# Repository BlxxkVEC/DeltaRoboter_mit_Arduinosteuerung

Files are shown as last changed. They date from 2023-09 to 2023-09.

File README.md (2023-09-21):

# DeltaRoboter_mit_Arduinosteuerung
 Ein Deltaroboter mit vielen Bauteilen aus dem 3D-Drucker mit einem Arduino zur Steuerung.

## README 

In diesem Repository sind alle Informationen und Dateien zu finden, um einen Deltaroboter (auch Plotbot genannt) zu bauen und mit einer grundlegenden Programmierung auszustatten. Dieses Projekt wurde nicht neu entwickelt, sondern es besteht eine grundlegende Bauanleitung von der Firma "B&R Industrial Automation". Diese beinhaltete jedoch viele preisintensive Bauteile und die Umsetzung war teilweise sehr umständlich. Daher haben wir einige Änderungen vorgenommen und eine neue Schritt-für-Schritt-Bauanleitung verfasst, mithilfe derer jeder das Projekt so durchführen kann, wie wir es getan haben. Die Bauanleitung enthält dafür die Links zu allen Bauteilen und eine detaillierte Beschreibung des Aufbaus. Zusätzlich gibt es eine Projektdokumentation, in welcher auf Schwierigkeiten und vorgenommene Änderungen eingegangen wird. In dem Ordner "3D Modelle" sind alle .stl-Dateien zu finden, die zum fertigen der Bauteile nötig sind. Diese Bauteile sind alle, welche wir in unserem Aufbau verwendet haben.
Bei dem Programm handelt es sich um ein Vorführprogramm. Dabei wird ein metallisches Objekt in Dauerschleife zwischen zwei Punkten umhertransportiert.

Der Ordner "Originaldateien von B&R" enthält alle Informationen und Dateien, welche wir anfangs von B&R erhalten haben, auf Grundlage derer der Roboter und dieses Projekt entstanden ist. Der Ordner enthält die originalen 3D-Modelle (wir haben diese umgearbeitet und Neue hinzugefügt), Zeichnungen von Bauteilen und die Bauanleitung, sowie den Guide für die Software. Der Ordner "Softwarebestandteile" beinhaltet das aktuelle Programm und praktische Bibliotheken für weitere Programme. Im Ordner "Informationsmaterial" sind ergänzende Dokumente zur Arbeitserleichterung enthalten.

Zusätzlich zu den .pdf-Varianten des Belegs und der Projektdokumentation sind hier auch die Links zum Anschauen der Dateien in Overleaf:

Projektdokumentation (Bauanleitung): https://de.overleaf.com/read/rbvrqmyprjpc

Beleg: https://de.overleaf.com/read/dvmrvychqrgd
komplett oben

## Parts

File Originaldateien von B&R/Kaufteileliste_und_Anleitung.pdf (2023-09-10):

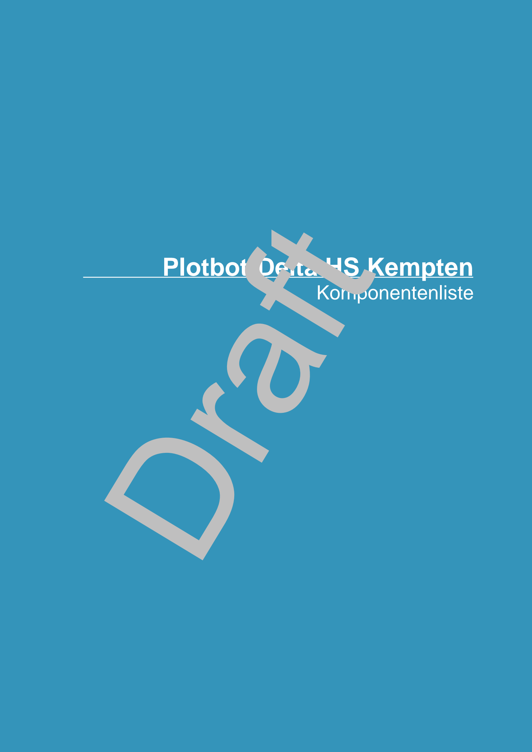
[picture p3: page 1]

# Plotbot-Delta HS Kempten

# Komponentenliste

## Inhaltsverzeichnis

## I Inhaltsverzeichnis

## Einleitung

## 1 Einleitung

Das folgende Dokument enthält Informationen zu den notwendigen Komponenten sowie zum Aufbau des 3 bzw. 4-Achsigen „Plotbot-Delta-Roboters“ der Hochschule Kempten.

Das Dokument wird frei verteilt und dient dem Leser als Anhaltspunkt für die Reproduktion des genannten Delta-Roboters. Das Dokument hat keinen Anspruch auf Vollständigkeit. Für die Richtigkeit der Angaben genauso wie für evtl. Schäden wird keinerlei Haftung übernommen.

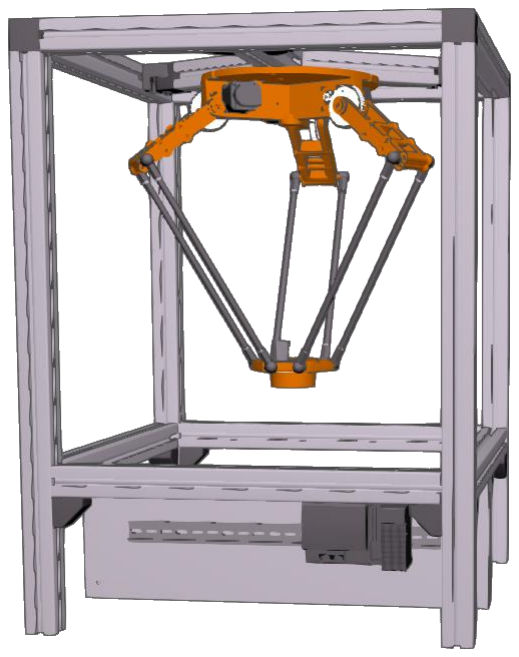
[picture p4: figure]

## 2 Informationen zum Druck der Bauteile

- Der getestete Drucker ist von der Marke Raise3D
- Das verwendete Filament ist PLA. (Alternativ: ABS, PETG, PLA plus)

### - Layerhöhe 0,15-0,2 (filigrane Teile) und 0,25-0,3 für die großen Strukturen - Schalenbreite: 1,2-1,6 mm - Füllgrad: 20-25 % mit kubischem Infill

## 3 Notwendige Komponenten

### 3.1 Liste der Zukaufteile

### 3.1.1 Sensoren

Nr. | Kompo-
nenten

Verwendung

Bezeichnung

Anzahl

Quelle | Preis
Summe
Stand
04.2020

### 1.1 Induktiver

Sensor

Referenzsensor der
Achsen

Autosen
AI811

3 https://autosen.com

58,59€

## Notwendige Komponenten

### 3.1.2 Zahnräder

Nr. | Kompo-
nenten

Verwendung

Bezeichnung

Anzahl

Quelle | Preis
Summe
Stand
04.2020
2.1 Zahnrad | groß | Unterset-zung Motor | Mädler 29405000 | 3 | www.maedler.de | 35,07€
2.2 Zahnrad | klein | Unterset-zung Motor | Zipperle SH12521HF | 3 | www.zipperle.de | 10,16€

### 3.1.3 Gleitlager und Kugelköpfe

Nr. | Komponen-
ten

Verwendung

Bezeichnung

Anzahl

Quelle | Preis
Summe
Stand
04.2020
3.1 Anlaufschei- | ben | Lagerung Gelenk 1 | igus JTM-1420-015 | 6 | www.igus.de | 16,32€
3.2 Kugelge- | lenke | Gelenke CFK Stangen | igus WGRM-08 | 12 | www.igus.de | 23,88€

### 3.1.4 CFK Stangen

Nr. | Komponen-
ten

Verwendung

Bezeichnung

Anzahl

Quelle | Preis
Summe
Stand
04.2020

### 4.1 CFK Stan-

gen

Kohlefaser-Rohr
10x8mm
1000 mm
(z.B.
Graupner
5221.10.8)

Zuschnitt
auf 300mm

2 Diverse Onlinehändler (z.B. http://www.dra- chen- markt.de/epages/DRA- CHEN- MARKT.sf/de_DE/?Ob- jectPath=/Shops/DRA- CHENMARKT/Pro- ducts/200-242)

30,96€

### 3.1.5 Kleber

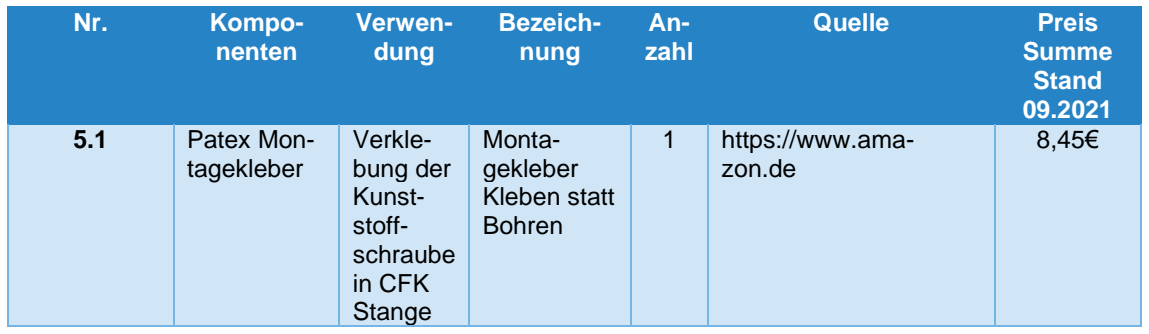
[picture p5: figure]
Kompo-; nenten; Verwen- dung; Bezeich- nung; An- zahl; Quelle; Preis; Summe Stand 09.2021; 5.1 Patex Mon- tagekleber; Verkle- bung der Kunst- stoff- schraube in CFK Stange; Monta- gekleber Kleben statt Bohren; https://www.ama-; zon.de

## Notwendige Komponenten

### 3.1.6 Schrauben

Nr. | Komponen-
ten

Verwendung

Bezeichnung

Anzahl | Quelle | Preis Summe Stand
| | 04.2020
6.1 Senkkopf- | schrauben | | M3X10 | 42
6.2 Senkkopf- | schrauben | | M3X16 | 42
6.3 Zylinder- | schrauben | | M4X45 | 9
6.4 Maden- | schrauben | Rizel -Mo-tor Siche-rung + | M3X4 DIN 916 | 6
6.5 | Zylinderstift | 1014-128 | A 3X16 DIN 7 | 3 - 6 | www.we-gertseder.com/
6.6 Kunststoff- | schrauben | Verbin-dung Ku-gelgelenk-Car-bonstab | DIN 933 M8X35 Kunststoff | 12 | https://www.horn-bach.de/shop/Sec hskantschraube-DIN-933-M8x35-mm-Polyamid-100-Stu-eck/8699894
6.7 Sechskant- | mutter (POM) | Feststel-lung / mi-nimale Einstel-lung der Länge | DIN 934 M8 Kunststoff | 12 | https://www.horn-bach.de/shop/Sec hskantmutter-DIN-934-M8-Poly-amid-50-Stu-eck/8682488

Kommentar – Anlaufscheiben: Die Anlaufscheiben sind dafür gedacht, dass die Kunststoffteile nur an einer kleinen reibungsarmen Fläche beim Betrieb in Kontakt kommen. Ohne würde der Kunststoff zu sehr bremsen.

### 3.1.7 Optionale Teile bei 4-Achs-Version

Nr. | Komponenten | Ver- wen- dung
Bezeichnung | An-
zahl
Quelle | Preis
Summe
Stand
04.2020
7.1 Ritzel | (POM) | Mädler 28202000 | 1 | https://www.ma-edler.de/Ar-ticle/28202000 | 0,63€
7.2 Zahnkranz | (POM) | Mädler 28204000 | 1 | https://www.ma-edler.de/Ar-ticle/28204000 | 1,30€
7.3 | Sicherungsring | Sicherungs-ring DIN 471 20mm | 1 | https://www.ma-edler.de/Ar-ticle/61742000 | 0,31€
7.4 | Motor | Nanotec Schrittmotor Nema 8 mit Stecker SC2018S0604 | 1 | https://de.nano-tec.com/pro-dukte/1839-sca2018-schritt-motor-mit-ste-cker-nema-8/ | 34,20€

## Notwendige Komponenten

### 7.5 Zylinderkopf-

schrauben

Befestigung
Motor

Größe passend zu verwendetem
Motor

### 3.2 B&R Komponenten

### 3.2.1 B&R Hardware Komponenten

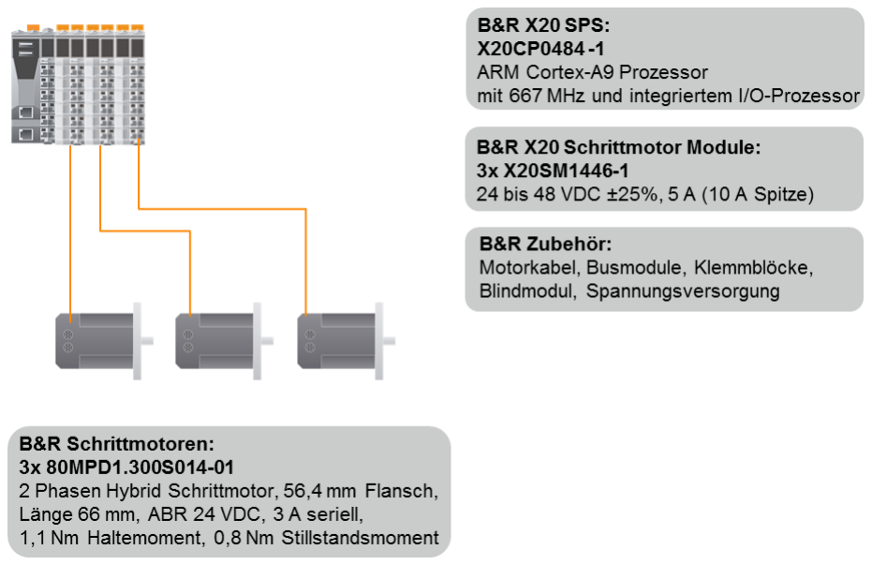
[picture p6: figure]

### 3.2.2 B&R Software Komponenten

- Education Technology Guard Basic Functions GF1460-10
Enthält Lizenzen der Technologiepakete mapp View, mapp Axis und mapp Services
- Education Technology Guard Robotic and CNC Functions MF4610-10
Enthält Lizenzen für eine parallele oder serielle Kinematik mit bis zu 4 bahngesteuerten Achsen
- B&R Automation Studio > 4.7
- mapp Technology > 5.10

### 3.3 Stückliste der 3D-Druck-Bauteile

Nr. | Anzahl | Dateibezeichnung
8.1 | 3 | Arm_Achse_Abstandshalter
8.2 | 3 | Arm_innere_Fuellung
8.3 | 3 | Grundplatte_Teilstück
8.4 | 3 | Steg Grundplatte_links
8.5 | 3 | Steg_Grundplatte_rechts
8.6 | 6 | Arm_Achse_Deckplatte
8.7 | 6 | Arm_seitliche_Platte
8.8 | 1 | Abstützung_Mitte
8.9 | 1 | Parallelplatte_4DOF
8.10 | 1 | Dreheinrichtung
8.11 | 3 | Sicherungsblock

## Notwendige Komponenten

### 3.4 Zu fertigenden Teile

### 3.4.1 Achse aus Aluminium für das erste Gelenk

Anzahl:3

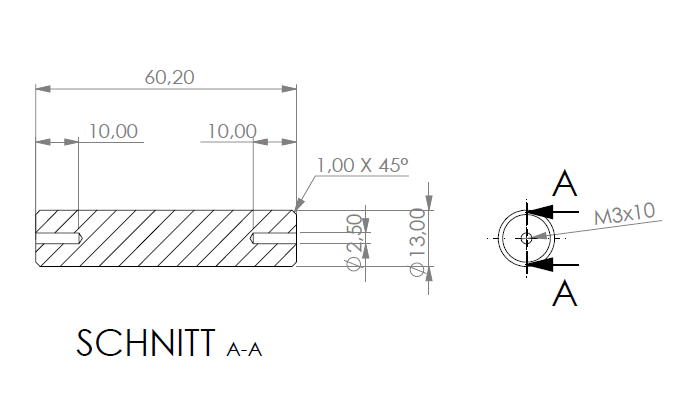
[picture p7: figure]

## Notwendige Komponenten

### 3.5 Zu modifizierende Kaufteile

### 3.5.1 Zahnräder

### 3.5.1.1 Bauteil 2.1 Mädler29405000

Anzahl 3
Die Skizze zeigt den Endzustand des Zahnrads

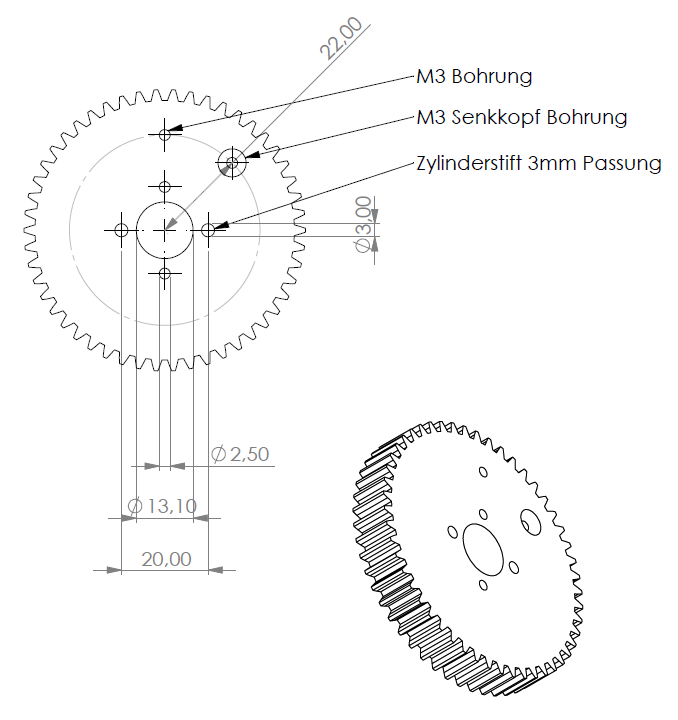
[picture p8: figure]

Kommentar:
Sowohl die „Bohrung M3“ wie auch die „M3 Senkkopf Bohrung“ dienen dem induktiven Sensor als Auslöser. Es ist nur eine der beiden Bohrungen notwendig.
Verwendet man die „M3 Bohrung“ steht der Roboter nach der Referenzfahrt in einer Position mit waagrechten Armen.
Bei Verwendung der anderen Position steht er etwas tiefer. Welche Position verwendet wird ist Geschmackssache.
Gleiches gilt für die Wahl der Schraube. Verwendet man eine Madenschraube, lässt sich diese in montiertem Zustand verstellen, sofern der Schraubenkopf in die dem Motor gegenüberliegende Richtung zeigt. Nachteil: Der Sensor muss auf einen kleineren Gegenstand reagieren. Verwendet man die Senkkopfschraube mit Kopf Richtung Motor. Ist das Schaltobjekt größer allerdings lässt sich die Schraube in montiertem Zustand nicht verstellen.

## Notwendige Komponenten

### 3.5.1.2 Zahnrad Mädler28204000 (Nur bei Verwendung der 4. Achse Notwendig)

Anzahl 1
Die Skizze zeigt den Endzustand des Zahnrads

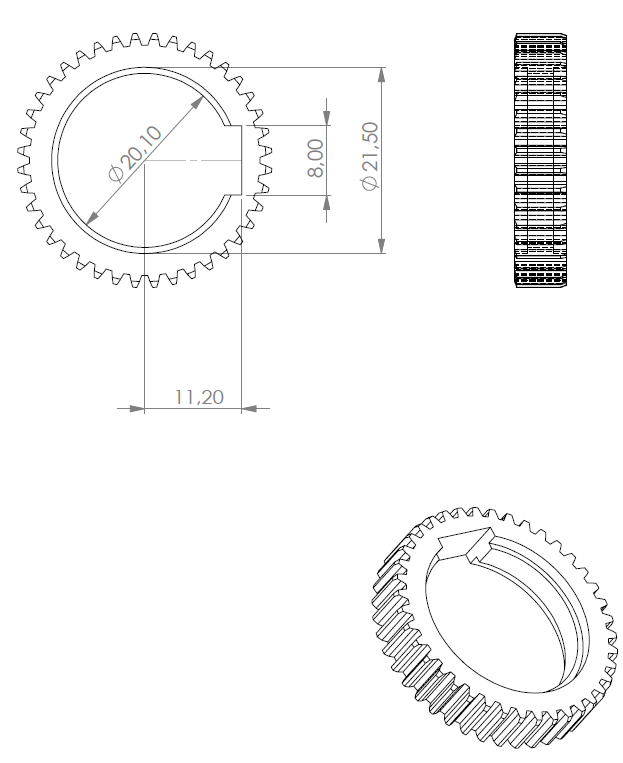
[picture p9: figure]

## Montage des Roboters

### 3.5.2 Sonstige Bauteile

- Evtl. Aufbohren der Zahnräder 2.2 auf das Maß der Motorwellen
- Bohrungen und Gewinde für die Madenschrauben setzen, die die Zahnräder 2.2 auf den Motorwellen arretieren.

## 4 Montage des Roboters

Schritt 1: M3 Gewinde in Steg_Grundplatte_links 8.4 und Steg_Grundplatte_rechts 8.5 schneiden

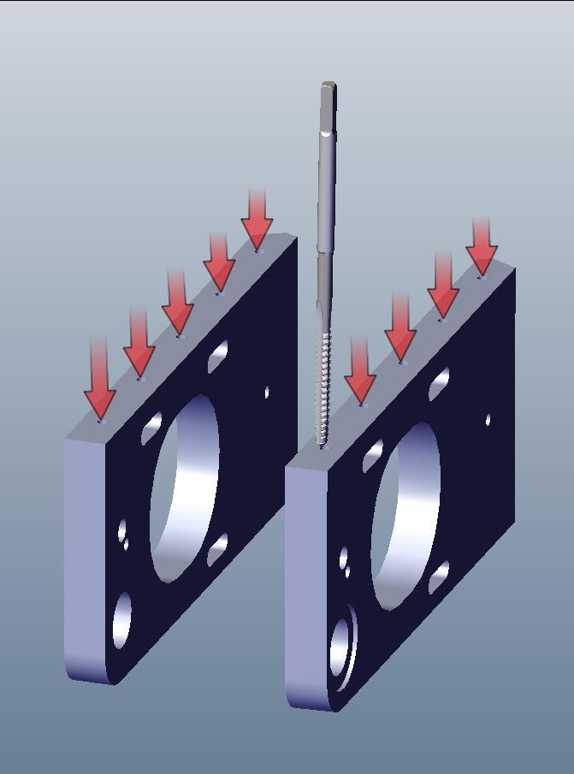
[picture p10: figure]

Schritt 2: Bauteile 8.4 und 8.5 mit Stiften 6.5 miteinander verbinden

Schritt 3 Zusammengefügte Bauteile 8.4 und 8.5 mit der Grundplatte verschrauben


Schritt 4: Abstützung_Mitte 8.8 montieren


Schritt 5: Induktiven Sensor 1.1 und Anlaufscheiben 3.1 montieren

Schritt 6: M3 Gewinde in Bauteil Arm_innere_Füllung 8.2 schneiden


Schritt 7: Bauteil 8.2 mit Arm_seitliche_Platte 8.7 (M3X10) und bearbeitetem Zahnrad 2.1 (M3X16 und Zylinderstift 6.5) verschrauben

Schritt 8: Gewinde M8 in Bohrung für Kugelkopf schneiden


Schritt 9: Bauteil Arm_innere_Fuellung 8.2 mit zweitem Bauteil Arm_seitliche_Platte 8.7 (M3X10) und bearbeitetem Zahnrad 2.1 (M3X16 und Zylinderstift 6.5) verschrauben. Dabei Distanzscheibe Arm_Achse_Abstandshalter 8.1 mit einsetzen. Im Anschluss auch auf dieser Seite ein Gewinde M8 vgl. Schritt 8 schneiden.

Schritt 10: Einschrauben der Kugelköpfe.


Schritt 11: Vormontierter Arm mit der Aluminiumachse an der Grundplatte befestigen und die „Arm_Achse_Deckplatte“ 8.6 mit M3X16 Schrauben auf beiden Seiten verschrauben.

Schritt 12: M8 Gewinde in Parallelplatte 8.9 schneiden und Kugelköpfe montieren.


Optional Schritt 13: Nema 8 Motor auf Parallelplatte 8.9 montieren und Zahnrad 7.1 am Motor befestigen. Überarbeitetes Zahnrad 7.2 in Dreheinrichtung 8.10 einpressen. Parallelplatte 8.9 und Dreheinrichtung 8.10 verbinden und mit Sicherungsring 7.3 verbinden.

Schritt 14: Verbinden der CFK Stäbe 4.1 mit den Kugelgelenken 3.2. Dazu werden die Köpfe der Kunststoffschrauben 6.6 abgesägt. Anschließend werden die Kugelgelenke 3.2 komplett auf die Kunststoffschrauben 6.6 geschraubt und von unten mit den Muttern 6.7 gekontert.


Die CFK Stäbe 4.1 werden auf die Länge von 300 mm zugeschnitten und die zuvor vorbereiteten Winkelgelenke 3.2 mit dem Gewinde in die Enden der CFK Stäbe 4.1 verklebt. Beim Verkleben ist auf die Ausrichtung der Winkelgelenke 3.2 zu achten. Diese müssen wie im untenstehenden Bild dargestellt in dieselbe Richtung orientiert sein. Als Kleber kann beispielsweise der Montagekleber von Patex 5.1 verwendet werden. Die verklebten CFK Stäbe 4.1 einen ganzen Tag aushärten lassen.

WICHTIG: Nicht zu viel Kleber auf das Gewinde auftragen, damit die Mutter nicht mit verklebt wird.


Schritt 15: Dreheinheit und Arme des Delta mit den vorbereiteten CFK Stäben inkl. Kugelschalen verbinden.

Schritt 16: Motoren mit aufgesetzten Zahnräder 2.2 in Motorhalterung einsetzen und mit Sicherungsblock 8.11 verschrauben. Dabei den Motor so einstellen, dass die Zahnräder im Eingriff sind.

Montage vollständig


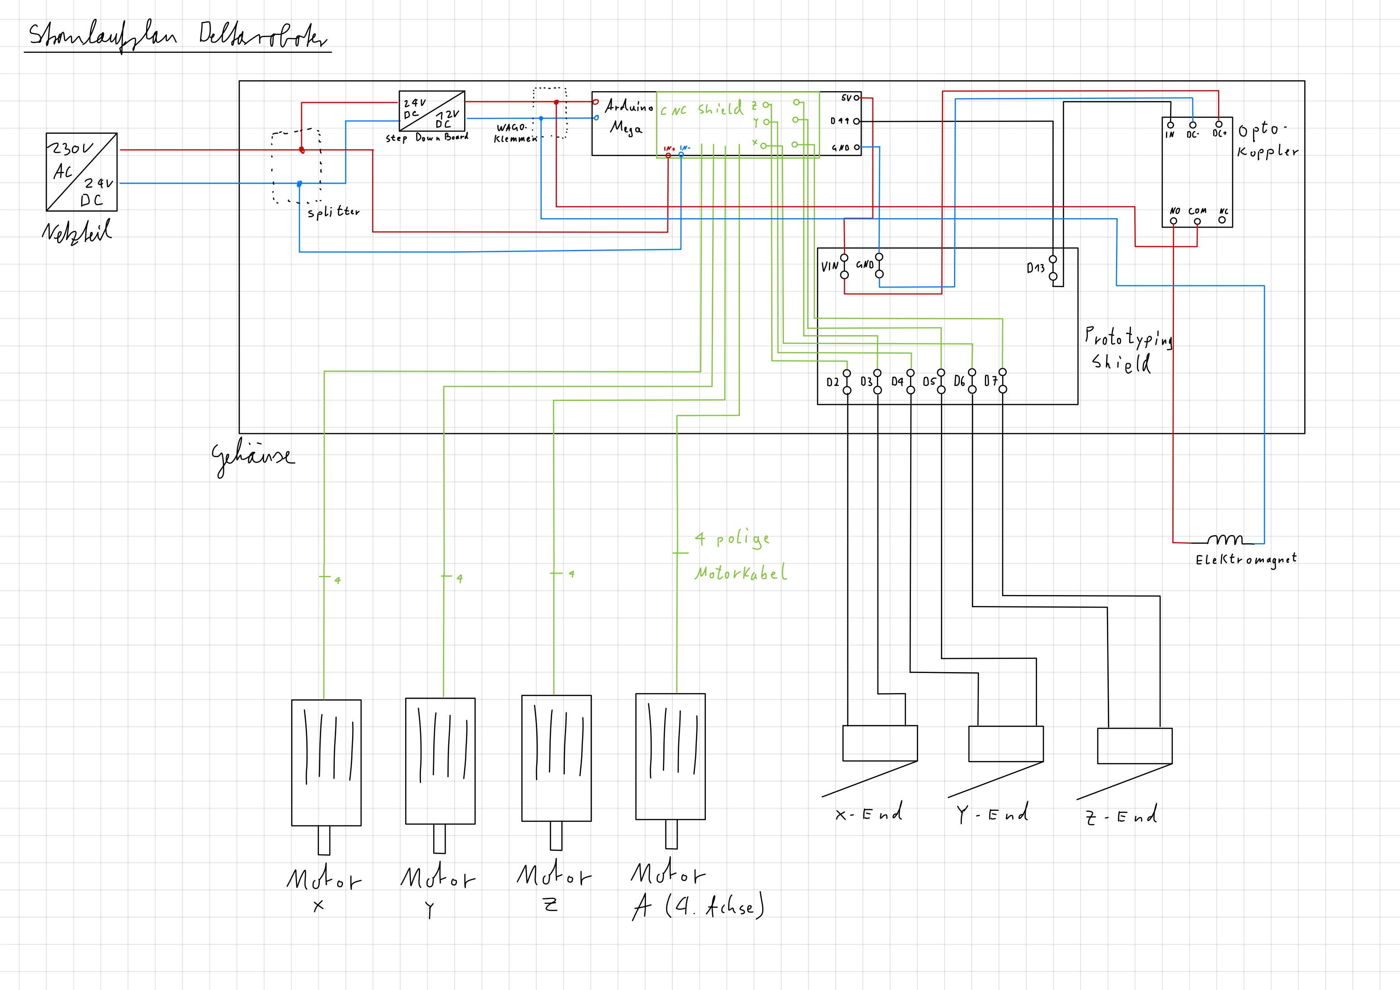
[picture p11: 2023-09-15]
Informationsmaterial/Stromlaufplan Delta-Roboter.jpg

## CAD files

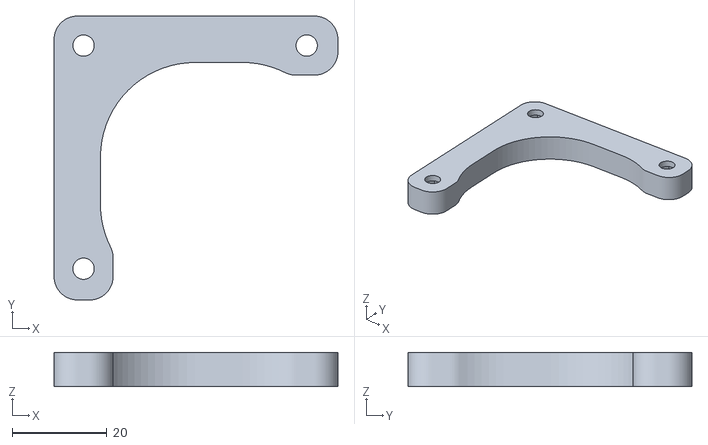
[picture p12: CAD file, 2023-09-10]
Originaldateien von B&R/B&R 3D-Modelle/3xSicherungsblock.STL
60.0 x 60.0 x 7.25

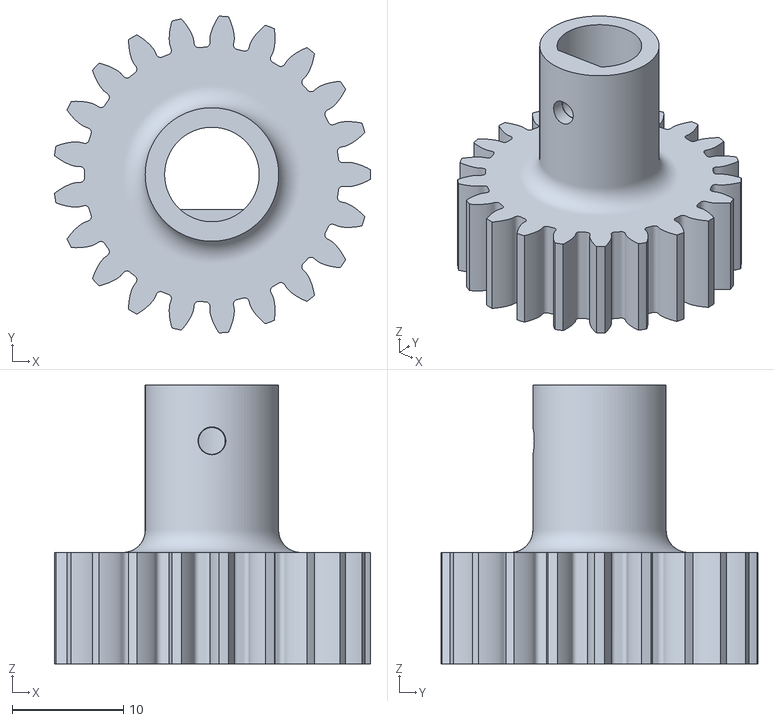
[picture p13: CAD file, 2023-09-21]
verwendete 3D Modelle/3xMotorzahnrad klein 8mm.stl
28.4 x 28.5 x 25.1

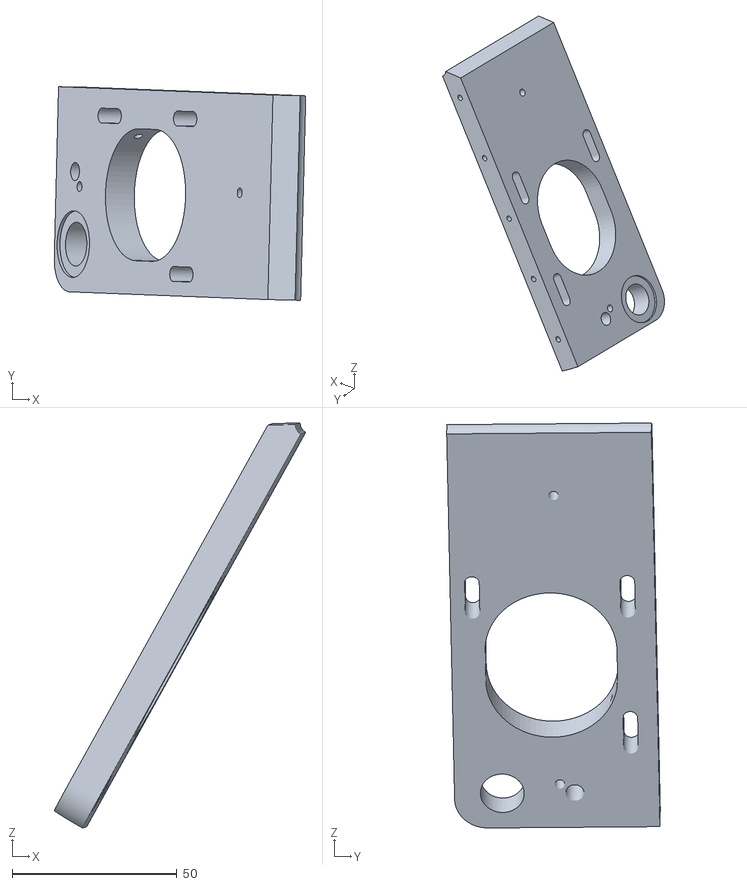
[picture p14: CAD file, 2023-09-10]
Originaldateien von B&R/B&R 3D-Modelle/3xSteg_Grundplatte_rechts.STL
76.2 x 64.7 x 122.7

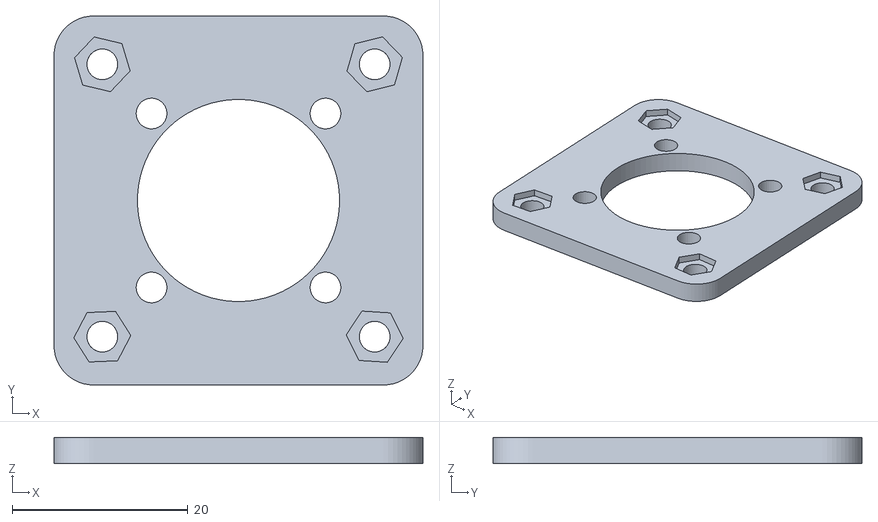
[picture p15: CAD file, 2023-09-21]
verwendete 3D Modelle/3xAdapterplatte Motor Planetengetriebe.stl
42.0 x 42.0 x 3.00

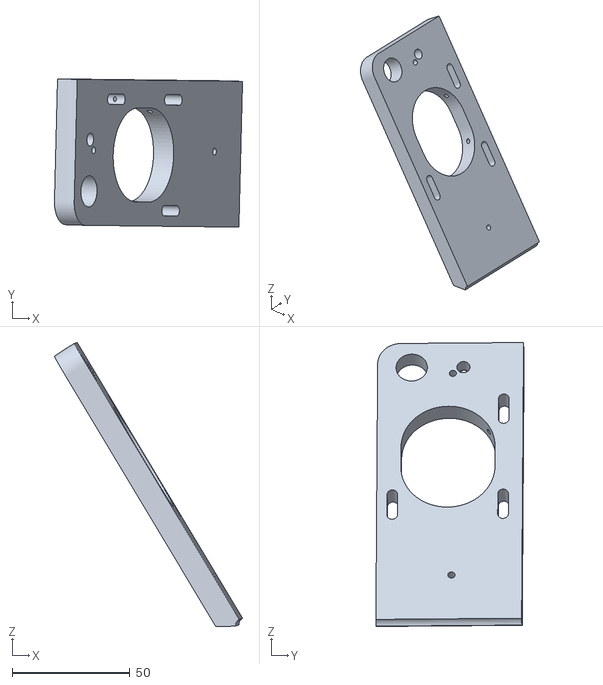
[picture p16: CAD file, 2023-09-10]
Originaldateien von B&R/B&R 3D-Modelle/3xSteg_Grundplatte_links.STL
80.0 x 63.1 x 120.8

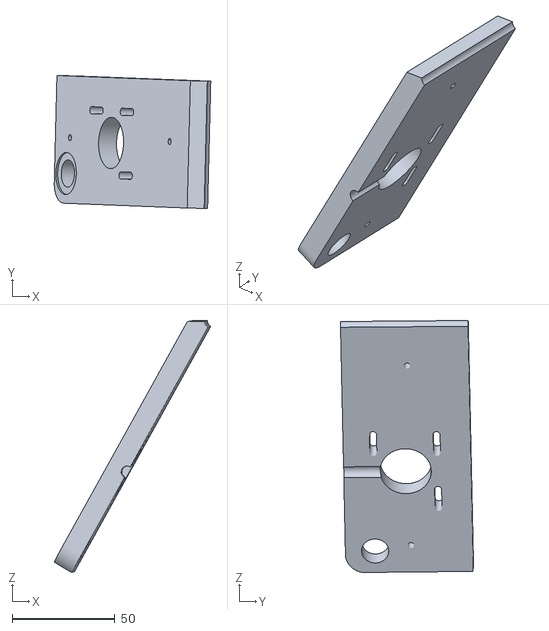
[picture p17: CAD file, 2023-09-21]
verwendete 3D Modelle/3x Motorplatte rechts überarbeitet (M3 zur Motormontage).stl
76.2 x 64.7 x 122.7

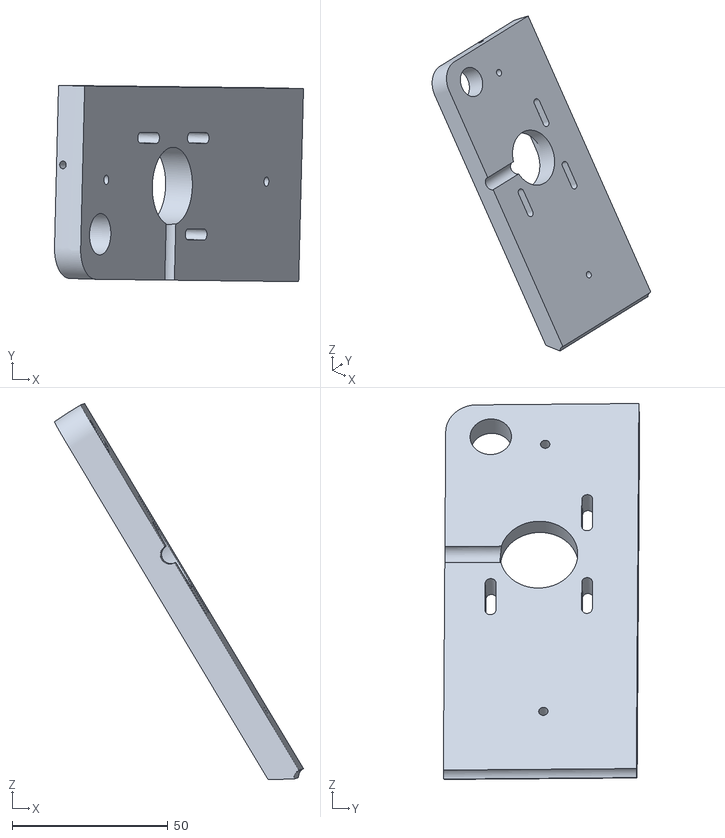
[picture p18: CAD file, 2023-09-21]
verwendete 3D Modelle/3x Motorplatte_links_überarbeitet (M3 zur Motormontage).stl
80.0 x 63.1 x 120.8

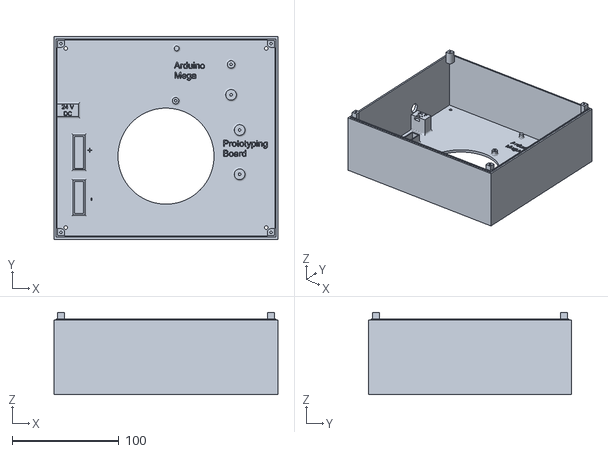
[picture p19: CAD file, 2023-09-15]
verwendete 3D Modelle/Gehäuse Elektronik _Träger.stl
210.0 x 190.0 x 77.0

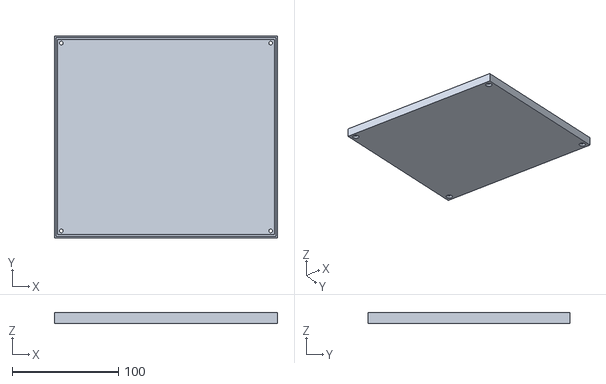
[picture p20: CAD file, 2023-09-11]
verwendete 3D Modelle/Gehäuse Elektronik_Deckel.stl
210.0 x 190.0 x 10.0

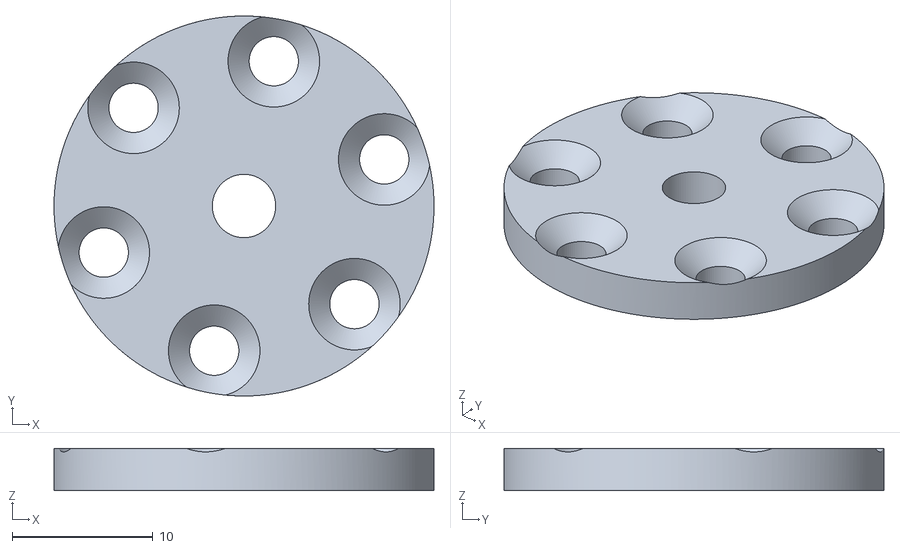
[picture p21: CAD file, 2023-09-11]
verwendete 3D Modelle/Magnethalterung .stl
27.0 x 27.0 x 3.00

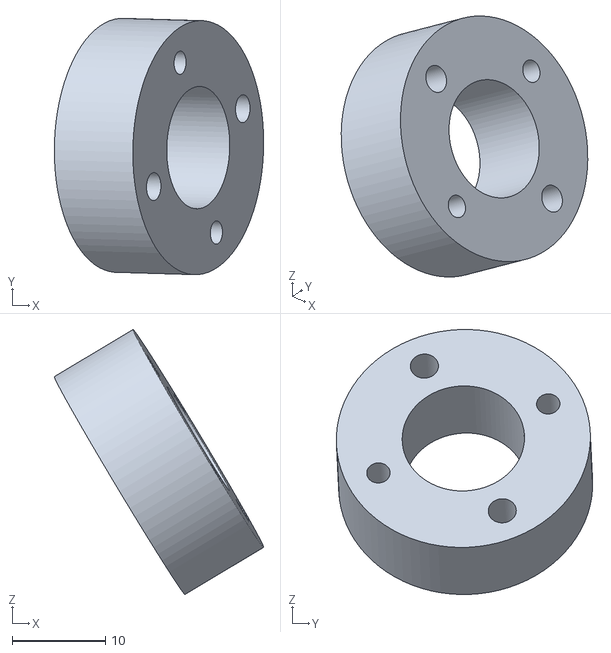
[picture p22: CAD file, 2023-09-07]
verwendete 3D Modelle/3xArm_Achse_Abstandshalter.STL
22.4 x 27.4 x 28.4

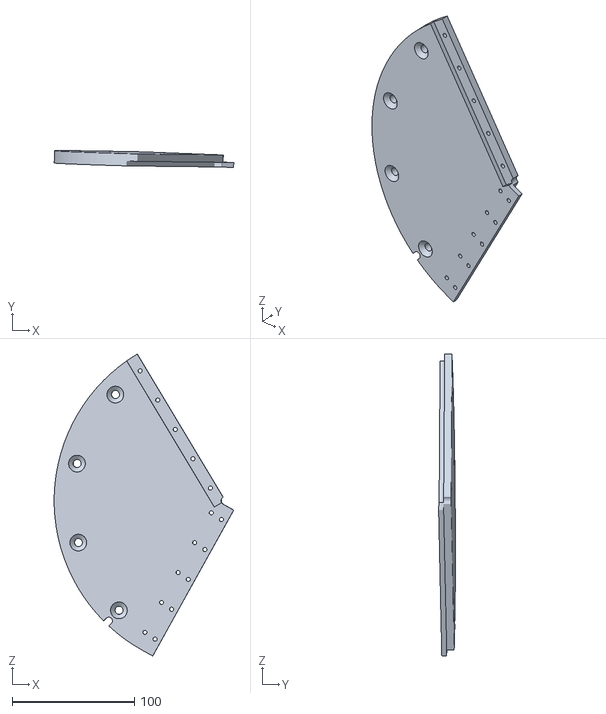
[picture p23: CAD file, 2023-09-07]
verwendete 3D Modelle/3x Trägerplatte_Teilstück.STL
147.1 x 13.8 x 247.4

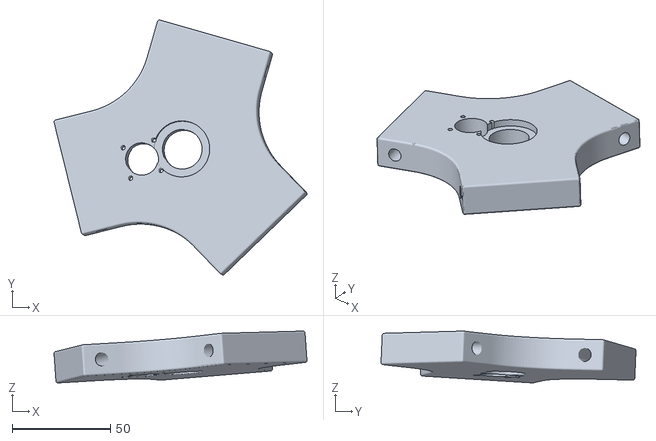
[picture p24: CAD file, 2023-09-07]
verwendete 3D Modelle/Parallelplatte.stl
128.7 x 129.7 x 26.4

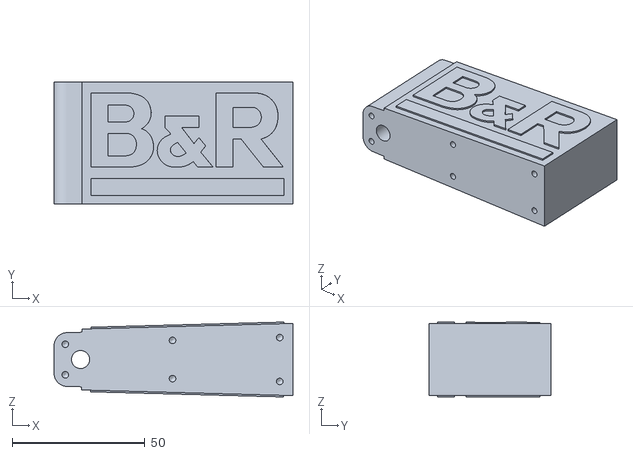
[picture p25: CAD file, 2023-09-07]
verwendete 3D Modelle/3xArm_innere_Fuellung.STL
90.0 x 46.0 x 28.2

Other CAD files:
verwendete 3D Modelle/6xArm_seitliche_Platte.STL
verwendete 3D Modelle/Achse.stl
verwendete 3D Modelle/Armzahnrad 29405000.stl
verwendete 3D Modelle/Zahnkranz (4. Achse).stl
verwendete 3D Modelle/6xArm_Achse_Deckplatte.STL
verwendete 3D Modelle/Abstützung_Mitte.STL
verwendete 3D Modelle/Dreheinrichtung.STL
verwendete 3D Modelle/Motorzahnrad 4. Achse 28202000.stl

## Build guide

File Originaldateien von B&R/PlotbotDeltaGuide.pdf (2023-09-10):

# PlotbotDelta@B&R

# Quick Start Guide

DeltaPlotbot@B&R
Quick Start Guide

Copyright © B&R - Änderungen vorbehalten PlotbotDeltaGuide.docx

14.11.22

B&R behält sich inhaltliche Änderungen ohne Ankündigung vor. Die Haftung durch B&R für drucktechnische Fehler sowie für sämtliche Angaben in diesem Dokument ist - soweit gesetzlich möglich – ausgeschlossen. Der Anwender ist für die Einhaltung aller relevanten und facheinschlägigen Sicherheitsmaßnahmen selbst verantwortlich. B&R weist darauf hin, dass die verwendeten Soft- und Hardwarebezeichnungen sowie Markennamen der jeweiligen Unternehmen den gesetzlichen Schutzvorschriften des Immaterialgüterrechts unterliegen.

Quick Start Guide

## Versionsstände

Version | Datum | Kommentar | Bearbeiter
1.00.0 | 13.11.2020 | Erste Ausgabe | Markus Straßer
2.00.0 | 24.11.2021 | Teach-Funktion, Datei Editor, Teach-Liste in Robotik Programm Konvertierung und laufende Verbesserungen | Markus Straßer

Tabelle 1: Versionsstände

## I Sicherheitshinweise und Symbole

Die Sicherheitshinweise werden im vorliegenden Dokument wie folgt gestaltet:

Warnung: Bei Missachtung der Sicherheitsvorschriften und -hinweise besteht die Gefahr schwerer Verletzungen oder großer Sachschäden.

Vorsicht: Bei Missachtung der Sicherheitsvorschriften und -hinweise besteht die Gefahr von Verletzungen oder von Sachschäden. Wichtige Angaben zur Vermeidung von Fehlfunktionen.

Information: Wichtige Angaben zur Vermeidung von Fehlfunktionen.

Quick Start Guide

## II Allgemeine Warnhinweise

Der Roboter darf nur unter der Berücksichtigung der DIN-EN-ISO 10218 Teil 1 und Teil 2 betrieben werden. Die Normen definieren Sicherheitsmaßnahmen für Industrieroboter wie notwendige Schutzzäune, Notfalleinrichtungen, Zugriffsschutz oder ähnliches.

Alle elektrischen Arbeiten müssen von einer berechtigten Person (Elektrofachkraft) durchgeführt wurden. Die Installation hat grundsätzlich in einem spannungsfreien Zustand zu erfolgen. Bei Missachtung kann es zu Kurzschlüssen oder elektrischen Schlägen kommen.

Sobald das Programm auf die Steuerung übertragen wurde, ist der Roboter in der Lage sich zu bewegen. Sorgen Sie dafür, dass der Roboter befestigt wurde und das keine Personen im Arbeitsbereich des Roboters sind. Ansonsten kann es zu Verletzungen und oder Beschädigungen des Roboters kommen!

Quick Start Guide | Einleitung

## Inhaltsverzeichnis

Quick Start Guide | Einleitung

## 1 Einleitung

In diesem Dokument wird gezeigt, wie man einen parallelen 3-Achs-Delta Roboter mit der B&R Steuerungsplattform und dem Automation Studio Projekt „PlotbotDelta“ in Betrieb nimmt.

## 2 Notwendige Softwareversionen

Software | Version
Automation Studio | V4.10.3.60
Automation Runtime | B4.91
mappMotion | 5.14
mappServices | 5.14
mappCockpit | 5.14
mappView | 5.14
SceneViewer | 4.1.0

Tabelle 2 Notwendige Versionen

## 3 Unterstütze Varianten des Roboters

3-Achs Delta Roboter

Schrittmotoren

Induktionssensoren für Referenzfahrt

Reichweite: 400 mm

Traglast: ca. 1000 g

Variante | Unterstütz

3-Achs Delta Plotbot – Ohne Geber 3-Achs Delta Plotbot – Mit Geber

Tabelle 3 Projekt Varianten

Abbildung 1 PlotbotDelta

Quick Start Guide | Notwendige B&R Komponenten

## 4 Notwendige B&R Komponenten

### 4.1 Hardware Komponenten

Anzahl | Artikelnummer | Optional | Beschreibung | Beschaffung
1 | X20CP0484-1 | | Steuerung | education.de@br-automation.com
1 | X20BB52 | | Busbasismodul
1 | X20PS9600 | | Spannungsversorgung
1 | X20TB12 | | Feldklemme
3 | X20SM1446-1 | | Schrittmotormodul
3 | X20BM31 | | Busmodul
3 | X20TB12 | | Feldklemme
1 | X20DI4371 | | Digitales Eingangsmodul
1 | X20DO6322 | | Digitales Ausgangsmodul
2 | X20BM11 | | Busmodul
2 | X20TB12 | | Feldklemme

Tabelle 4 B&R Komponenten

Die Hardwarekomponenten müssen in der gleichen Reihenfolge wie im Automation Studio Projekt gesteckt werden (siehe Abbildung 2).

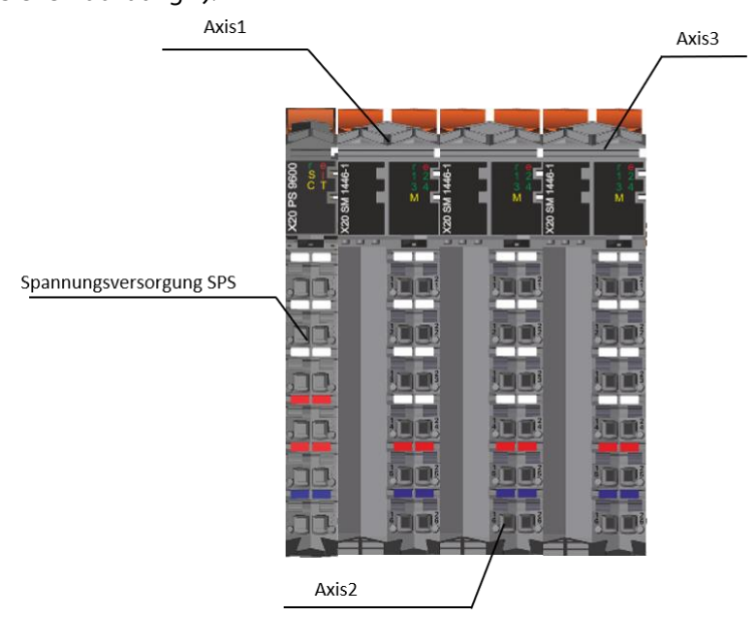
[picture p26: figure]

Abbildung 2: Reihenfolge der Hardwaremodule

### 4.2 B&R Lizenzen

Für den Betrieb des Roboters für Lehr- und Forschungszwecke werden keine Lizenzen verlangt.

Quick Start Guide

Optionale Komponenten für die Spannungsversorgung

## 5 Optionale Komponenten für die Spannungsversorgung

Für einen laborgerechten Einsatz wird empfohlen Niedervoltsteckverbindungen und Tischnetzteile zu verwenden, damit die Komponenten Berührungssicher sind. Sollte der Roboter einen Schaltschrank bekommen, kann auch ein herkömmliches 24V Hutschienen Netzteil und Klemmblöcke zur Spannungsverteilung verwendet werden.

Anzahl | Artikelnummer | Beschreibung | Beschaffung | Link
2 | DC-2G21-XL | Niedervolt Buchse

Conrad Electronic

Elhttps://www.conrad.de/de/p/bkl-electronic-niedervolt-anschlusskabel-niedervolt-buchse-offenes-ende-5-5-mm-2-5-mm-2-00-m-1-st-1082739.html (https://www.conrad.de/de/p/bkl-electronic-niedervolt-anschlusskabel-niedervolt-buchse-offenes-ende-5-5-mm-2-5-mm-2-00-m-1-st-1082739.html)

1 | 1371050 | Niedervolt Y-Verteiler

https://www.conrad.de/de/p/voltcraft-niedervolt-anschlusskabel-niedervoltbuchse-niedervolt-stecker-5-5-mm-2-1-mm-5-5-mm-2-1-mm-1-10-m-1-st-1371050.html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 (https://www.conrad.de/de/p/voltcraft-niedervolt-anschlusskabel-niedervolt-buchse-niedervolt-stecker-5-5-mm-2-1-mm-5-5-mm-2-1-mm-1-10-m-1-st-1371050.html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)

2 | DC14-M | Niedervolt Stecker

https://www.conrad.de/de/p/tru-componentsdc14-m-niedervolt-steckverbinder-stecker-gerade-5-5-mm-2-1-mm-1-st-1570700.html (https://www.conrad.de/de/p/tru-components-dc14-m-niedervolt-steckverbinder-stecker-gerade-5-5-mm-2-1-mm-1-st-1570700.html)

1 | GST280A24-C6P | Tischnetzteil 11,67 A

https://www.conrad.de/de/p/mean-wellgst280a24-c6p-tischnetzteilfestspannung-24-v-dc-11-67-a-280-08-w-1439261.html (https://www.conrad.de/de/p/mean-well-gst280a24-c6p-tischnetzteil-festspannung-24-v-dc-11-67-a-280-08-w-1439261.html)

1 | 1008230 | Kaltgeräte Kabel

https://www.conrad.de/de/p/hawa-1008230-
kaltgeraete-anschlusskabelschwarz-2-00-m-621535.html (https://www.conrad.de/de/p/hawa-1008230-kaltgeraete-anschlusskabel-schwarz-2-00-m-621535.html)
Tabelle 5 Sonstige Komponenten

## 6 Verdrahtung

Alle elektrischen Arbeiten müssen von einer berechtigten Person (Elektrofachkraft) durchgeführt wurden. Die Installation hat grundsätzlich in einem spannungsfreien Zustand zu erfolgen. Bei Missachtung kann es zu Kurzschlüssen oder elektrischen Schlägen kommen.

### 6.1 Spannungsversorgung

Im Folgenden werden die Arbeitsschritte für die Verdrahtung unter Verwendung der optionalen Komponenten aus Kapitel 5 beschrieben:

1. Stecker am Netzteil mit einem Seitenschneider abschneiden. 2,5 – 3,0 cm entmanteln. Die vier Adern des Kabels abisolieren und mit Aderendhülsen versehen.
2. Die Adern in die Niedervolt-Stecker einführen und festschrauben
Pol | Aderfarbe
+ | Rot, Blau
- Weiß, Schwarz

Tabelle 6 Netzteil Adernbelegung

Quick Start Guide | Verdrahtung
3. Um die Niedervolt-Buchsen auf die X20 Module anzubringen, das Kabel auf die gewünschte Länge zuschneiden und das rote Kabel auf Pin 15, sowie das rot-schwarze Kabel auf Pin 16 verbinden.
4. Da das Hardwaresetup aus insgesamt 4 X20 Scheiben besteht, die eine direkte Spannungsversorgung benötigen, aber nur 2 Niedervolt-Buchsen zur Verfügung stehen, müssen zwei der Module per Drahtbrücke versorgt werden. Somit hängt die Spannungsversorgung der SPS und der Achse 1 an einer Zuleitung, sowie die der Achsen 2 und 3.

Die Drahtbrücke wird mittels einer Zwillings-Aderendhülse realisiert. Außerdem ist es notwendig noch eine zusätzliche Drahtbrücke am PS9600 anzubringen (siehe Abbildung 3).

Die rechte Seite der Klemmen wird für die Spannungsversorgung der Induktionssensoren am Roboter genutzt.

Kanal | Aderfarbe | Pin
+24VDC | Rot | 15
GND | Rot-Schwarz | 16

Tabelle 7 Spannungsversorgung X20 Module

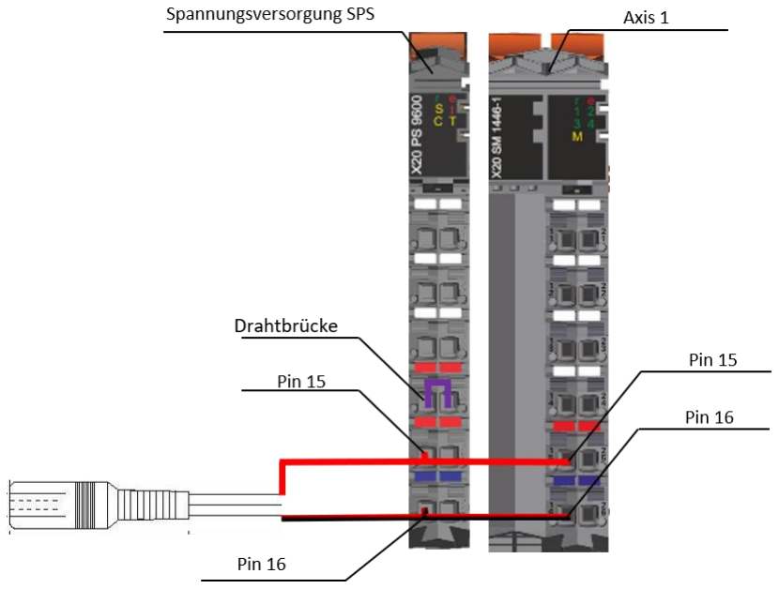
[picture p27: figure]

Abbildung 3: Versorgung SPS und Achse 1

Quick Start Guide | Verdrahtung

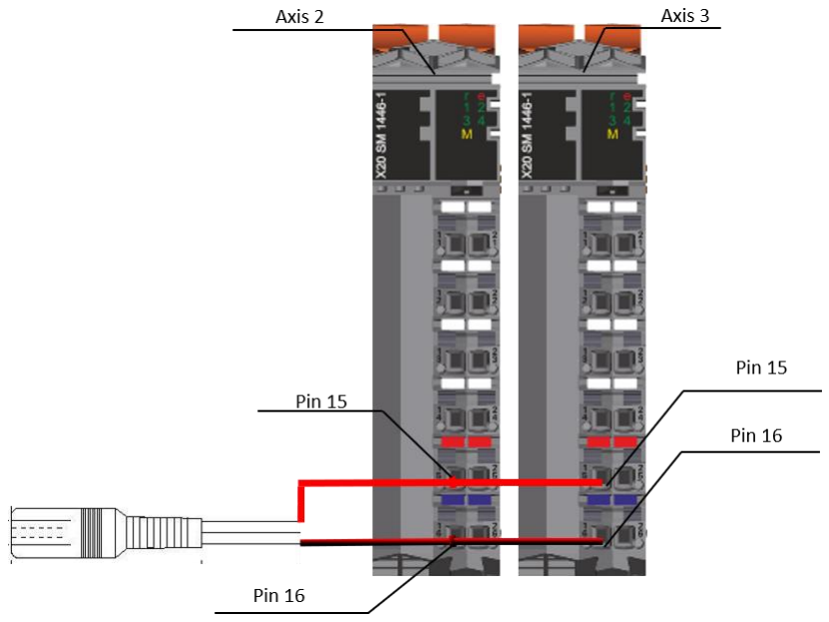
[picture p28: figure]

Abbildung 4: Versorgung Achse 2 und 3

5. Sind alle Arbeitsschritte erledigt kann das Netzteil über den Y-Verteiler mit allen Steckern verbunden werden. Fangen alle Module an grün zu blinken, wurde die Verdrahtung der Spannungsversorgung fehlerfrei durchgeführt.

Alle weiteren elektrischen Arbeiten müssen wieder im spannungsfreien Zustand durchgeführt werden!

### 6.2 Motor

Bei der Verbindung der Motorkabel zu den X20 Schrittmotor Modulen ist darauf zu achten, dass die Achsen in der richtigen Reihenfolge verbunden werden. Je nach Reihenfolge ändert sich die Ausrichtung des Koordinatensystems.
In diesem Dokument werden die Motoren auch als Achsen bzw. als Axis bezeichnet. Als Achse wird dabei nicht nur der Motor selbst, sondern das eigentliche Drehgelenk am Roboter verstanden.

Quick Start Guide | Verdrahtung

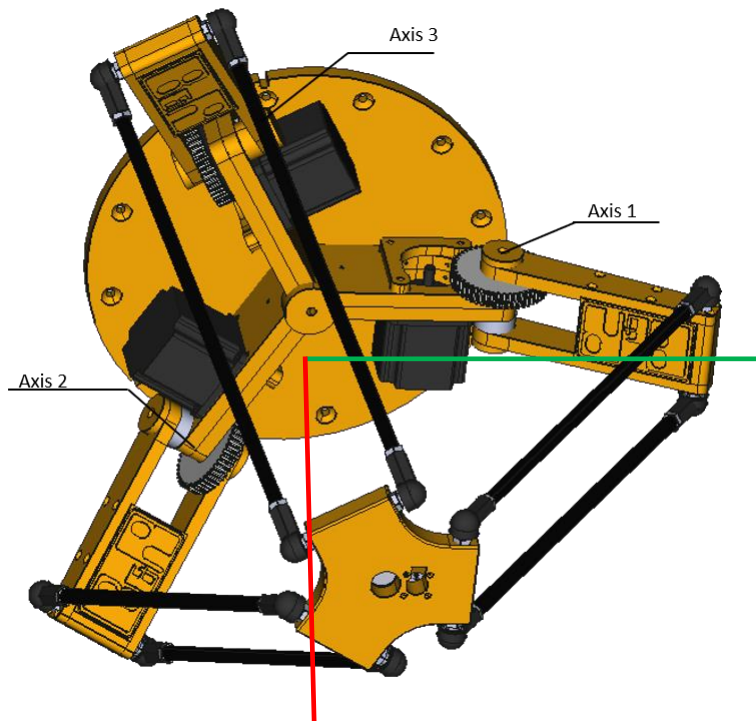
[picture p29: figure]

Abbildung 5 Achsenbezeichnung

Die vier verschiedenen Adern des Konfektionierten B&R Motorkabels müssen wie folgt mit den X20SM1446-1 Modulen verbunden werden.

Kanal | Adernfarbe | Pin
A | Schwarz | 13
A\ | Grau | 23
B | Braun | 14
B\ | Blau | 24

Tabelle 8 Aderbelegung Motoren

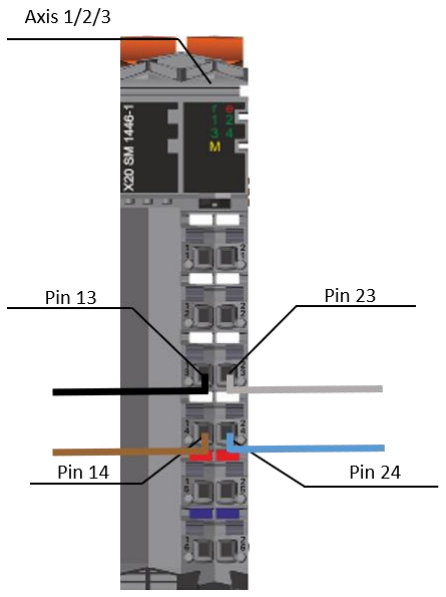
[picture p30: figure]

Abbildung 6 Motoranschluss

Y

X

Quick Start Guide | Verdrahtung

### 6.3 Referenzschalter

Die Kabel der Referenzschalter müssen in die davor vorgesehen Verschraubung am Roboter befestigt werden. Achten Sie darauf, dass die Sensoren der jeweiligen Achsen auf die korrekte X20 Schrittmotorkarte gelegt wird.
Nachdem die Kabel entmantelt und abisoliert wurden müssen diese wie folgt mit der X20SM1446-1 verbunden werden.
Kanal | Adernfarbe | Pin
Signal | Schwarz | 22
+24 VDC | Braun | 25
GND | Blau | 26

Tabelle 9 Belegung Referenzsensoren

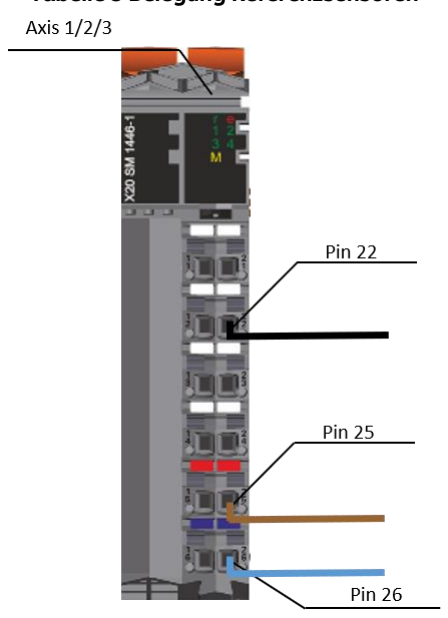
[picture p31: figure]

Abbildung 7 Anschluss Referenzschalter

Quick Start Guide | Mechanische Anpassungen

## 7 Mechanische Anpassungen

In den Standard Einstellungen befindet sich der Ursprung des Koordinaten Systems auf der Höhe der Gelenke des Robotersockels. Sollte sich durch das Anschrauben eines Rahmens die Basishöhe verändern. Kann dies im Automation Studio Projekt angepasst werden.

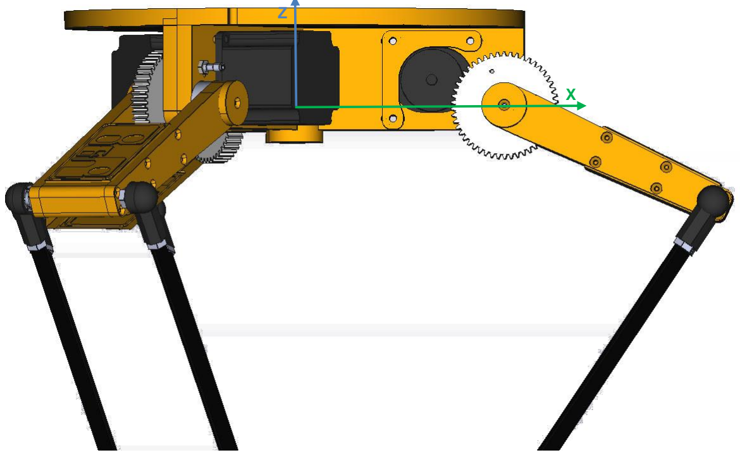
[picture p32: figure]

Abbildung 8 Koordinaten Ursprung

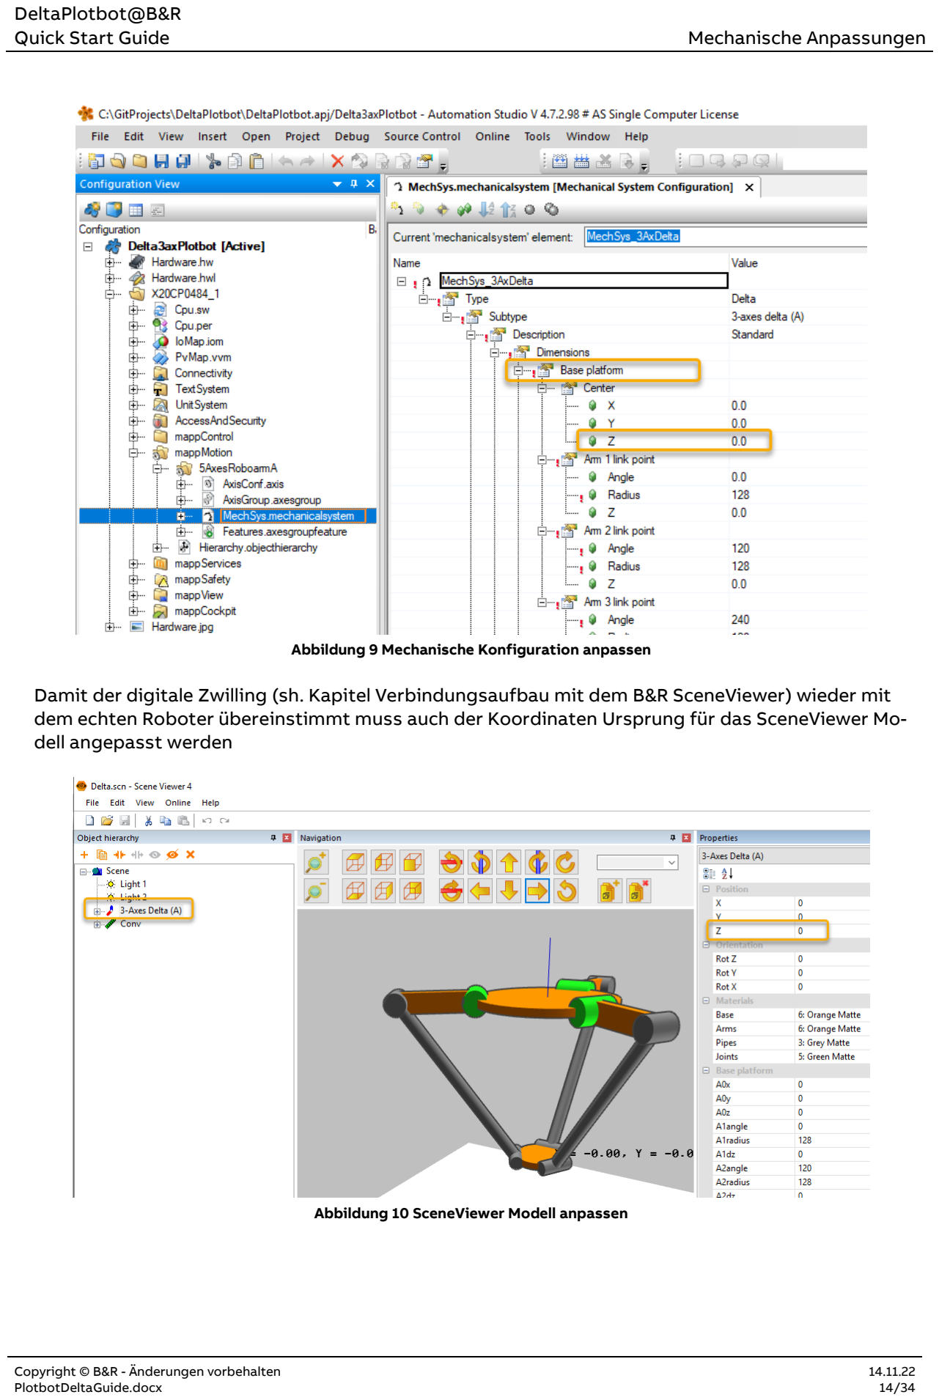
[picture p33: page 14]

Quick Start Guide | Mechanische Anpassungen

Abbildung 9 Mechanische Konfiguration anpassen

Damit der digitale Zwilling (sh. Kapitel Verbindungsaufbau mit dem B&R SceneViewer) wieder mit dem echten Roboter übereinstimmt muss auch der Koordinaten Ursprung für das SceneViewer Modell angepasst werden

Abbildung 10 SceneViewer Modell anpassen

Quick Start Guide | Inbetriebnahme

## 8 Inbetriebnahme

Der Roboter darf nur unter der Berücksichtigung der DIN-EN-ISO 10218 Teil 1 und Teil 2 betrieben werden. Die Normen definieren Sicherheitsmaßnahmen für Industrieroboter wie notwendige Schutzzäune, Notfalleinrichtungen, Zugriffsschutz oder ähnliches.

### 8.1 Lokales Netzwerk

In den Standardeinstellungen des Projekts hat die Ethernetschnittstelle (IF2) der Steuerung die IP-Adresse 192.168.0.1.
Sollte die Steuerung über ein existierendes DHCP Netzwerk mit dem PC/Laptop verbunden werden, wird empfohlen die IP-Einstellungen der Steuerung zu ändern.

### 8.2 Online Verbindung

Vergewissern Sie sich, dass die Simulationsschaltfläche nicht gedrückt ist.

Um eine Verbindung zur Steuerung aufzubauen, klicken Sie in der Menüleiste auf „Online“ und danach „Einstellungen“.
Wird die Steuerung zum ersten Mal mit einer Software versehen, kann mit der Schaltfläche „Durchsuchen“ das Netzwerk nach aktiven B&R Steuerung gesucht werden.

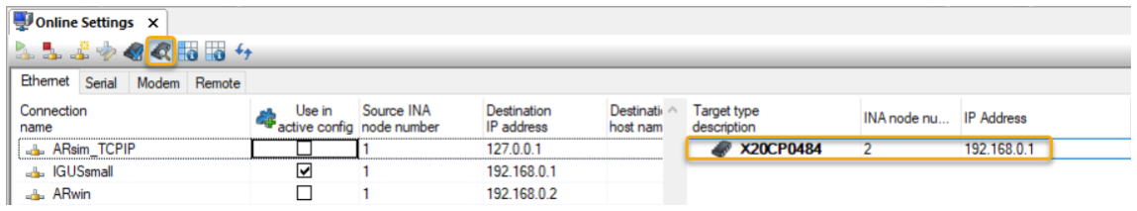
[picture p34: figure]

Abbildung 11 B&R Steuerung suchen
Wird die Steuerung mit einem „Warnschild“ dargestellt, muss per Rechtsklick und danach „IP-Einstellungen ändern“ folgendes eingestellt werden.

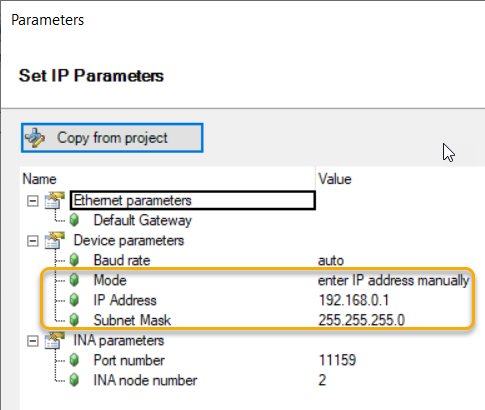
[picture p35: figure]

Abbildung 12 IP-Adresse ändern

Quick Start Guide | Inbetriebnahme

Bitte beachten Sie, dass Ihr PC im gleichen Netzwerk wie die Steuerung sein muss. Ihr PC sollte demnach die gleiche Subnetzmaske und eine IP-Adresse im Bereich 192.168.0. 2 – 192.168.0.254 besitzen. Ändern Sie die PC IP-Adresse nur wenn das Automation Studio geschlossen ist.

Sind PC und Steuerung im gleichen Netzwerk verschwindet das „Warnschild“. Per Drag&Drop wird die Verbindung in das linke Fenster gezogen und mit der Schaltfläche „Verbinden“ aktiv geschalten.

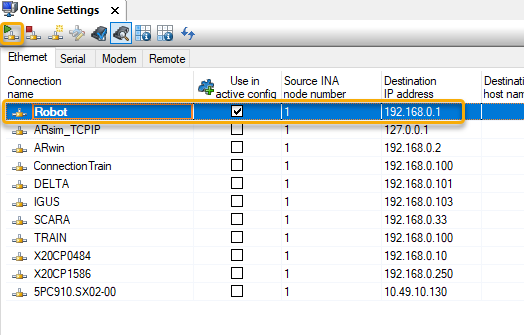
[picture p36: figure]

Abbildung 13 Mit Steuerung verbinden

Ist in der Statusleiste ein grünes „RUN“ zu sehen, konnte die Verbindung zu Steuerung erfolgreich
hergestellt | werden.

### 8.3 Transfer

Sobald das Programm auf die Steuerung übertragen wurde, ist der Roboter in der Lage sich zu bewegen. Sorgen Sie dafür, dass der Roboter befestigt wurde und das keine Personen im Arbeitsbereich des Roboters sind. Ansonsten kann es zu Verletzungen und oder Beschädigungen des Roboters kommen!

Mit einem Klick auf die Schaltfläche „Übertragen“ | wird das Projekt kompiliert. Sind
keine Fehler aufgetreten, wird der Transfer Dialog geöffnet.

Quick Start Guide | Inbetriebnahme

Klicken Sie auf das Zahnradsymbol.

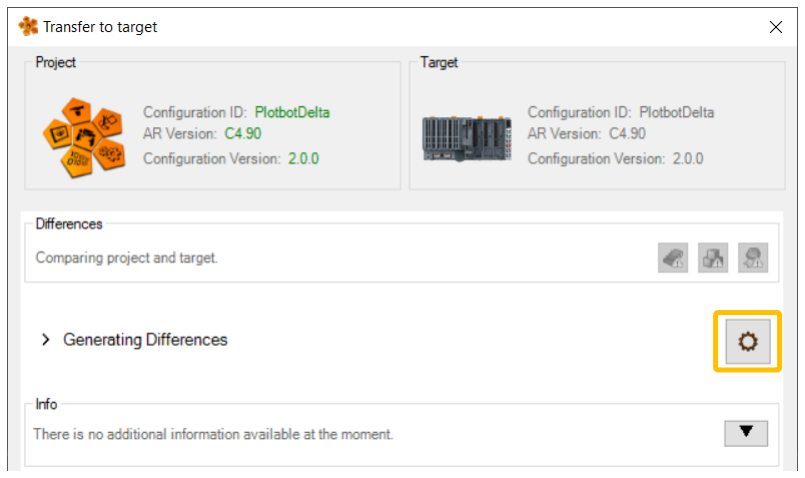
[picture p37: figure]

Abbildung 14 Projekt übertragen

Setzen Sie anschließend den Haken bei „Dateien in USER-Partition kopieren“ sowie „Vorhandene Dateien überschreiben“ und geben dabei folgenden Pfad an.

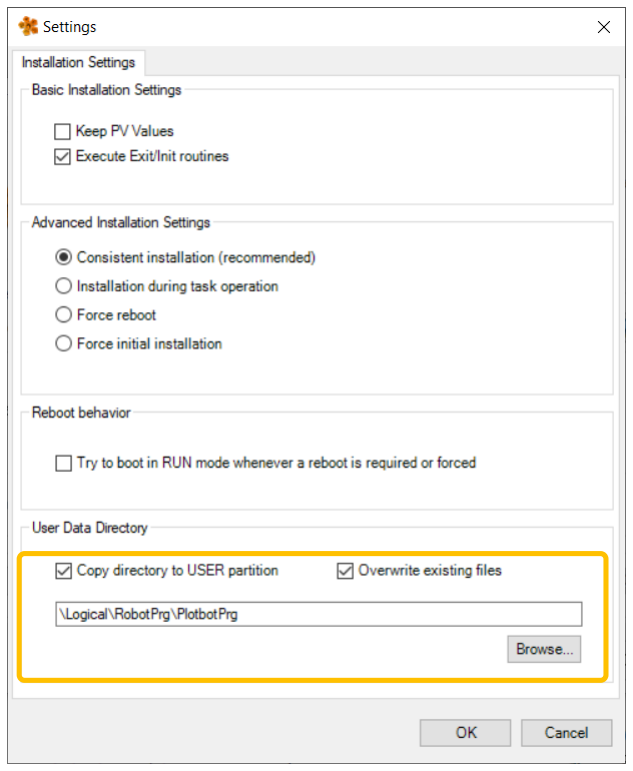
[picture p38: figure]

Abbildung 15 Übertragungs Einstellungen

Bestätigen Sie die gemachten Einstellungen und starten Sie die Übertragungsprozedur.

Quick Start Guide | Inbetriebnahme

Beim erstmaligen Übertragen kann es aufgrund des Firmware Updates an allen Komponenten zu einer erhöhten Hochlaufzeit der Steuerung kommen.

### 8.4 Einschalten und Referenzfahrt

Der Roboter kann nun über die Visualisierung bedient werden. Über die Schaltfläche „Power“ werden die Motoren eingeschaltet.

Über die Schaltfläche „Home“ wird die Referenzfahrt gestartet. Ist die Referenzfahrt abgeschlossen sollte sich der Roboter in dieser Position befinden.

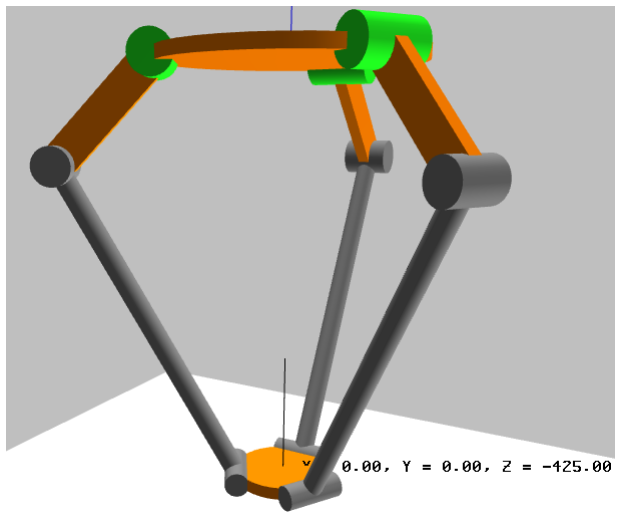
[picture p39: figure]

Abbildung 16 Roboter Nulllage

Sollte sich der Roboter nicht in diese Position bewegen, stoppen Sie die Bewegung so schnell wie möglich mit der Schaltfläche „Stop“ oder schalten die Spannungsversorgung ab! Mögliche Fehlerursache könnte die falsche Verdrahtung der Motoren oder Induktionssensoren sein!

Quick Start Guide | Simulation

## 9 Simulation

Um mit dem Roboterprojekt auch „Offline“ also ohne reale Hardware arbeiten zu können, wurde eine Simulationsumgebung integriert. Diese besteht aus der in das Automation Studio eingebettete Laufzeitumgebung ARsim und einem 3D Abbild des Roboters in dem B&R Tool SceneViewer.

### 9.1 Aktivieren der ARsim

Die ARsim kann im Projekt mit der Schaltfläche | gestartet werden.
Sobald in der Statusleiste die Steuerung im RUN ist | kann das Projekt auf das
Zielsystem mit der Schaltfläche | übertragen werden.

Nachdem das Projekt kompiliert wurde, wird anschießend der Transfer Dialog geöffnet. Mit einem Klick auf die Schaltfläche Transfer werden alle Bestandteile auf die ARsim übertragen.
Details zum Kompilieren und Übertragen können der Automation Studio Hilfe entnommen werden.

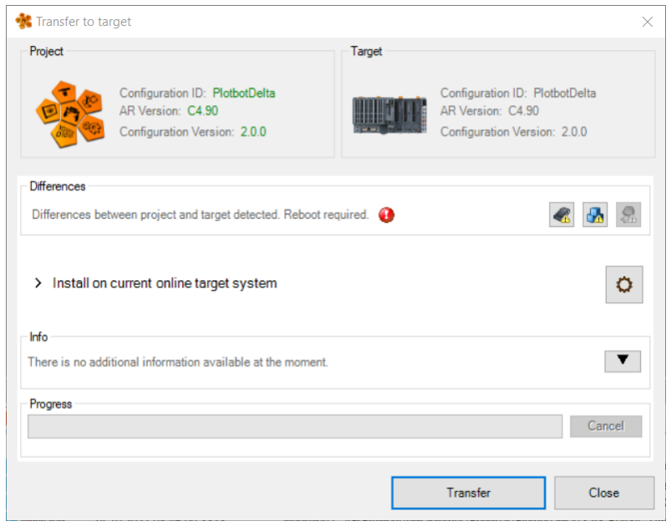
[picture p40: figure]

Abbildung 17 Projekt aus ARsim übertragen

Ist der Fortschrittsbalken bei 100% angekommen ist das Roboter-Projekt einsatzbereit. Informationen zur Bedienung des Roboters sind in Kapitel Visualisierung zu finden.

### 9.2 Verbindungsaufbau mit dem B&R SceneViewer

Für eine visualisiertes Echtzeitabbild des Roboters wird das B&R Tool Scene Viewer verwendet. Das dazugehörige Modell kann in der Logical View unter dem Ordner „DigitalTwin“ geöffnet werden.

Quick Start Guide | Simulation

Abbildung 18 Datei Simulationsmodell

Um das Modell mit der Steuerung zu verbinden, muss über das Menü „Online“ und der Schaltfläche „OPC-UA“ die Funktion „Connect“ gewählt werden.

Abbildung 19 SceneViewer Verbindung

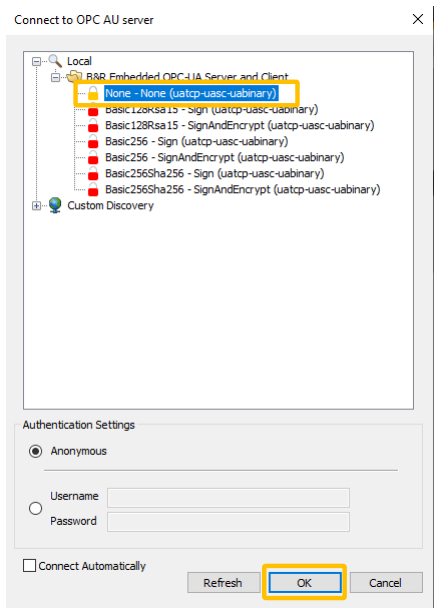
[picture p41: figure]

Abbildung 20 Verbindungseinstellungen

Die Verbindung mit der Steuerung wird anschließend über die Bestätigung mit „OK“ aufgebaut. Nachdem der Dialog mit der Schaltfläche bestätigt wurde zeigt die Status Leiste des Scene Viewer . Damit sind Modell und Steuerung erfolgreich verbunden und können genutzt werden.

Quick Start Guide | Robotik Programme

## 10 Robotik Programme

Im Projekt sind bereits einige Beispiel Roboter-Programme in der Logical View zu finden..

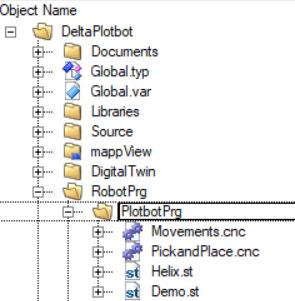
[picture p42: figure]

Abbildung 21 Roboter-Programme

Die B&R Steuerungen unterstützen in der Standardkonfiguration für Koordinierte Achsbewegungen zwei unterschiedliche Sprachvarianten.

G-Code

Strukturierter Text

Welche Befehle verwendet werden können und wie deren Sprachsyntax aussieht kann der Automation Studio Hilfe entnommen werden.

Neue Roboter-Programme können über die Toolbox als Element „Neue Datei“ hinzugefügt werden. Dazu muss die Dateiendung richtig angegeben werden. Programme mit der Sprache Strukturierter Text bekommen die Endung „.st“. G-Code Programme bekommen die Endung „.cnc“.

Quick Start Guide | Visualisierung

## 11 Visualisierung

Die Visualisierung kann sowohl bei einer simulierten Steuerung als auch bei einer real vorhandenen Steuerung verwendet werden. Es ändert sich lediglich die URL im Browser. Als Browser am PC muss Google Chrome verwendet werden. Die Visualisierung lässt sich auch auf einem von B&R erhältlichem Display anzeigen.

Steuerungsart | URL
Simulation | http://127.0.0.1:81/index.html?visuId=VisDelta
Hardware | http://192.168.0.1:81/index.html?visuId=VisDelta

Tabelle 10 URL Visualisierung

### 11.1 Authentifizierung

Für einige Funktionen auf der Bedienoberfläche ist die Eingabe von Benutzernamen und Passwort notwendig:

Benutzer: Admin
Passwort: admin

### 11.2 Startseite

Die Visualisierung ist in mehrere Teile aufgeteilt und bietet den Nutzer unterschiedliche Möglichkeiten den Roboter zu bedienen.

Die angebotenen Bedienmodi mit dieser Visualisierung sind:

Robotik Programme abfahren (G-Code und Strukturierter Text)

Tippbetrieb für jede Koordinate

Kartesische Einzelpunkte anfahren

Teach Modus

Eine genauere Beschreibung der verschiedenen Bedienmodi entnehmen Sie den folgenden Abschnitten.

In der oberen Leiste, der Visualisierung, befinden sich Informationen zur Uhrzeit, Datum sowie Schaltflächen für Sprache, Einheitensystem, anstehende Fehlermeldungen und einem Benutzer Login. Darunter befinden sich Textfelder, die die aktuellen Roboter Zustände anzeigen. Hier können auch mehrere Zustände gleichzeitig aktiv sein. Auf der linken Seite befinden sich die Schaltflächen für die unterschiedliche Bedienmodi.
In der unteren Leiste befinden sich Zahlenfelder zur Anzeige der aktuellen kartesischen Position des Roboters.
Die Startseite selbst zeigt ein 3D Modell des Roboters.

Quick Start Guide | Visualisierung

Abbildung 22 Startseite

Roboter Zustände

Aktuelle Position

Sprache/Einheit

Fehlermeldungen

Login

Bedienseiten

Quick Start Guide | Visualisierung

### 11.3 Automatischer Modus

Im automatischen Modus können Robotik Programme ausgeführt werden. Einige Demo Robotik Programme sind bereits im Projekt enthalten. Um ein Robotik Programm ausführen zu können, muss der Roboter eingeschaltet und referenziert sein.

Abbildung 23 Automatischer Modus

Referenzieren

Roboter
An/Aus

Programm
starten

Programm
stoppen

Roboter-Programme

Quick Start Guide | Visualisierung

Mit dem Programm Monitor können die aktiven Programmzeilen eines Robotik Programms angesehen werden.

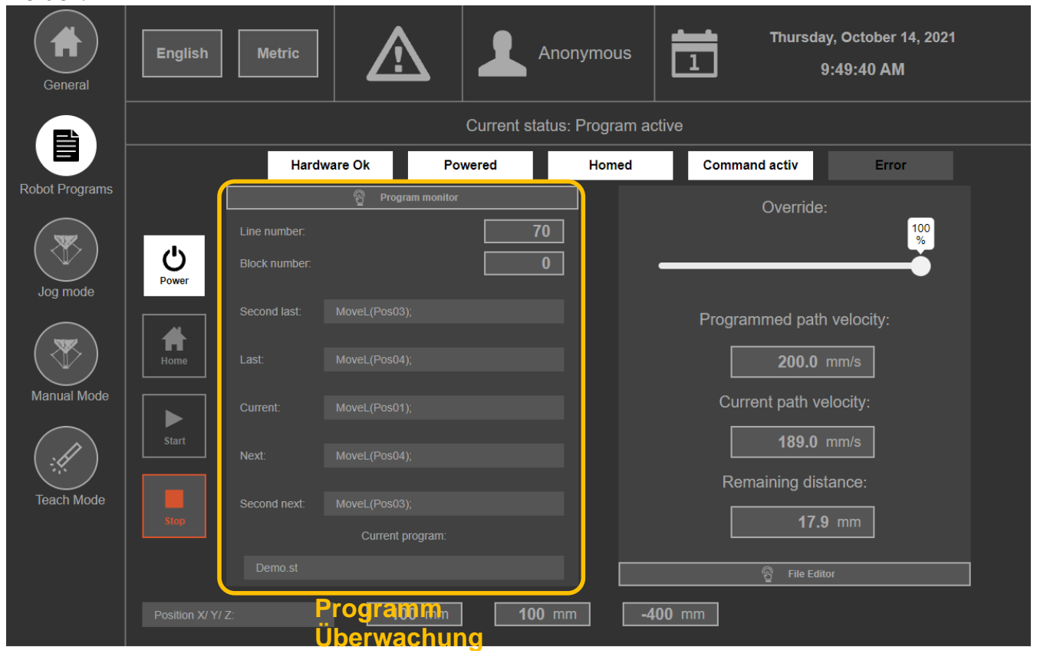
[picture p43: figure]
Programm Überwachung

Abbildung 24 Programm Monitor

Quick Start Guide | Visualisierung

Mit dem Programm Editor, können bestehende Robotik Programme editiert oder neue Programme

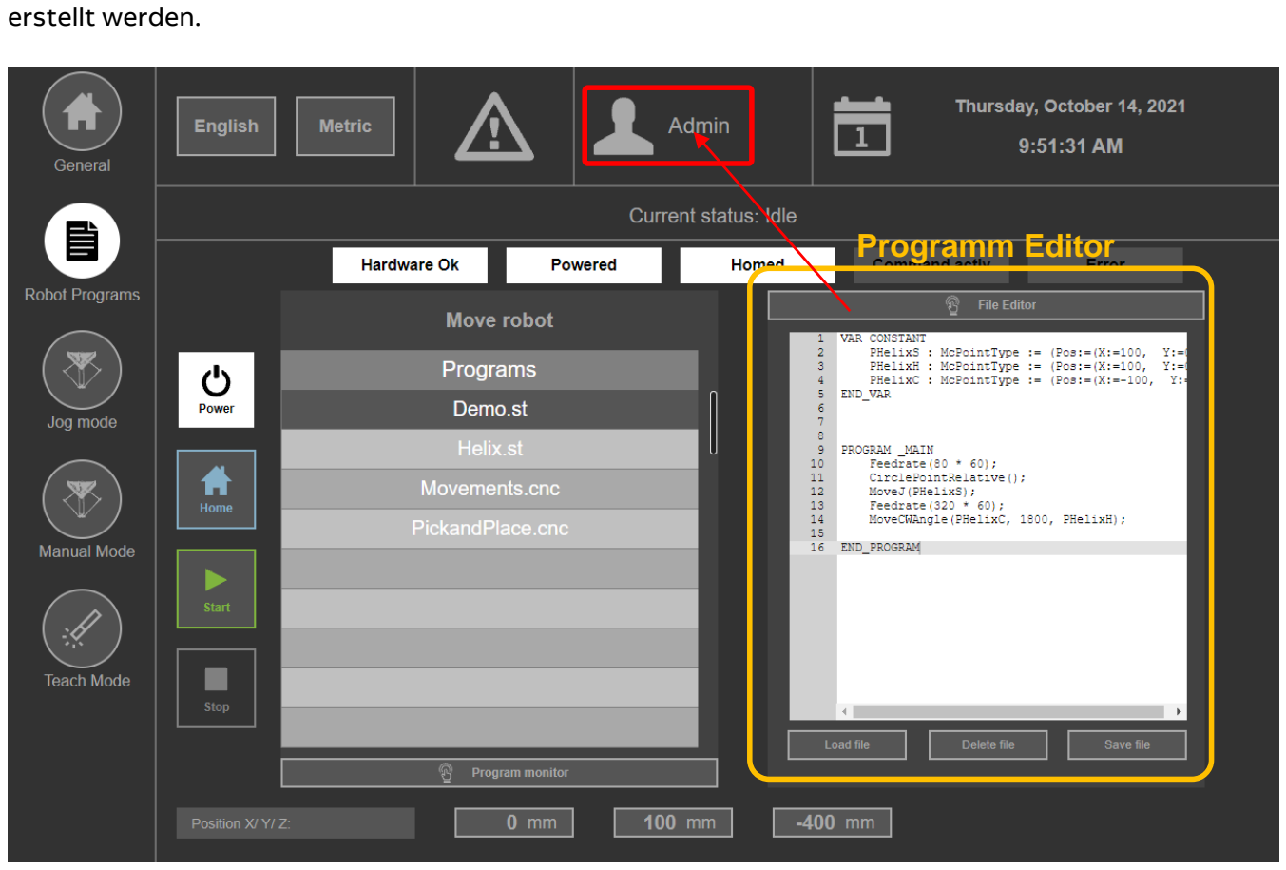
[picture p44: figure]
erstellt werden.; Programm Editor

Abbildung 25 Programm Editor

Quick Start Guide | Visualisierung

### 11.4 Tippbetrieb

Auf der Seite Jog werden die Koordinaten einzeln angewählt und mittels der Schaltflächen in unterschiedliche Richtungen verfahren. Der Roboter muss dafür ebenfalls eingeschaltet und referenziert sein.

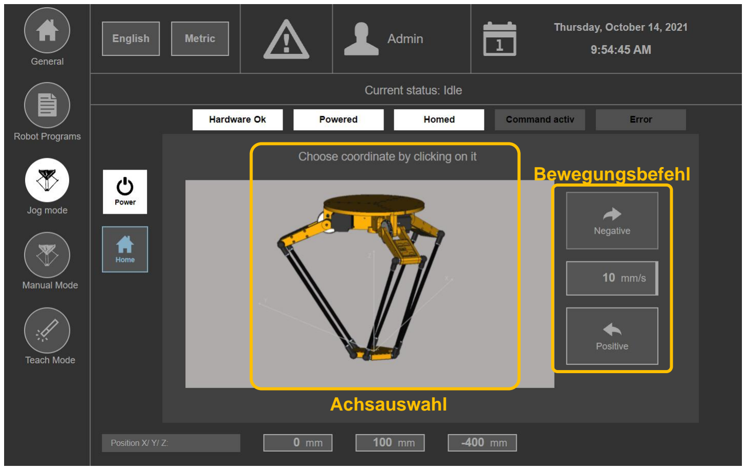
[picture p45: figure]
Achsauswahl; Bewegungsbefehl

Abbildung 26 Tippbetrieb

Quick Start Guide | Visualisierung

### 11.5 Manueller Modus

Auf der Seite manueller Modus können kartesische Koordinaten direkt oder linear angefahren werden.

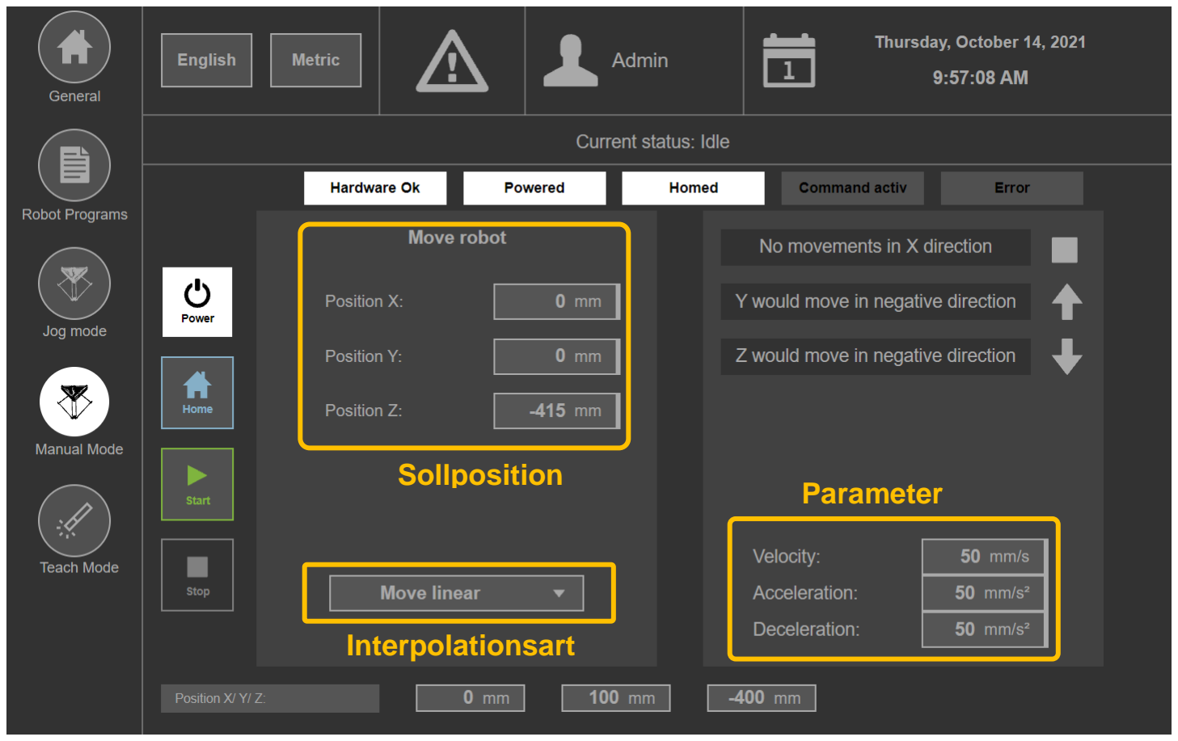
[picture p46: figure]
Sollposition; Interpolationsart; Parameter

Abbildung 27 Manueller Modus

Quick Start Guide | Visualisierung

### 11.6 Lern Modus

Auf der Seite Lern Modus, können Punkte manuell angefahren und sich in einer Liste gemerkt werden. Die Liste kann neben den Punkten auch mit Pausen und Greifer Aktionen gefüllt werden, um eine Pick and Place Anwendung zu realisieren. In die Liste werden die Ist Positionen aufgenommen. Die Liste kann abgespielt werden oder auch ein ST oder G-Code File generiert werden, dass unter den Robotik Programmen wiederum editier- und abspielbar ist.

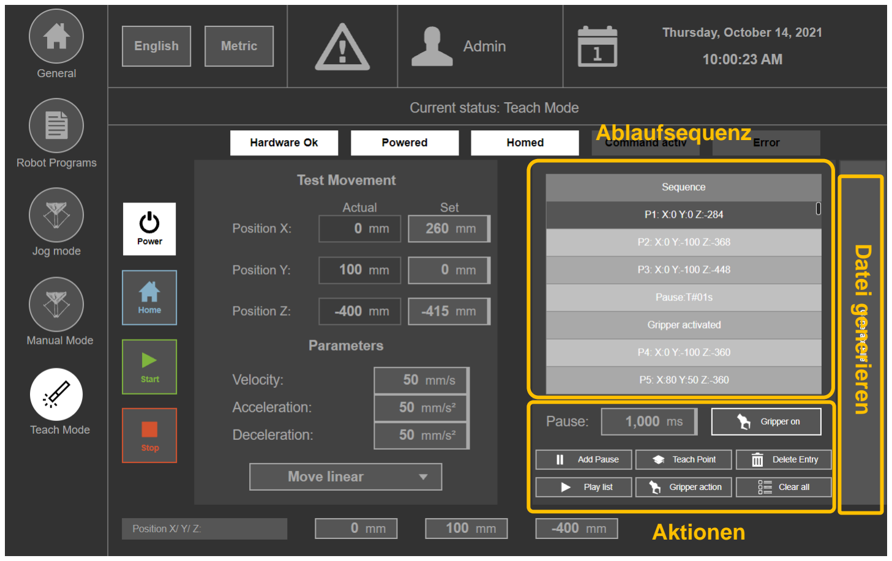
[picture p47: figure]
Ablaufsequenz; Aktionen; Datei generieren

Abbildung 28 Lern-Modus

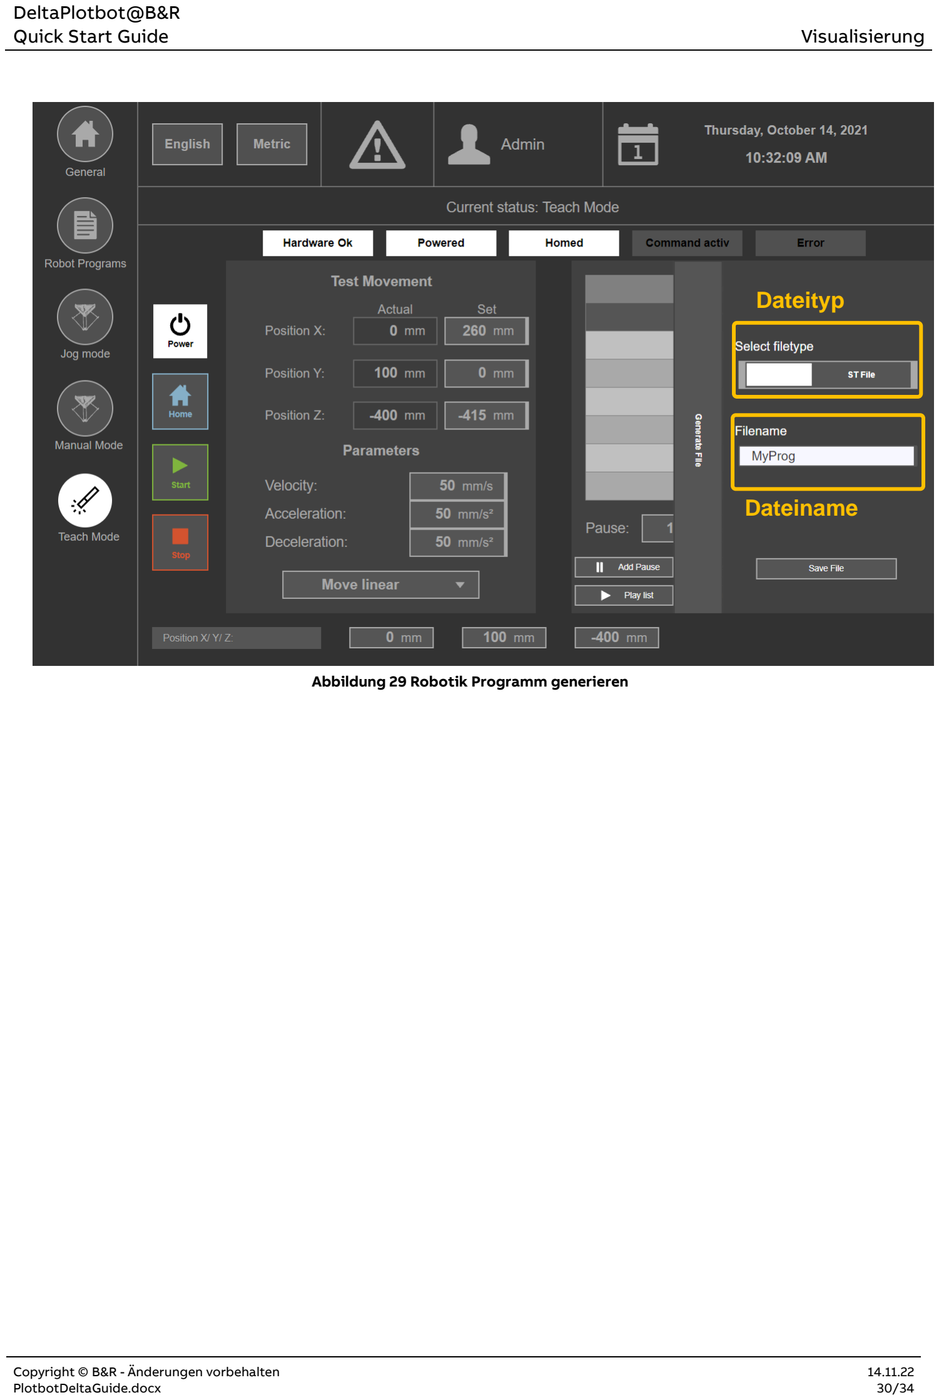
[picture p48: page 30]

Quick Start Guide | Visualisierung

Abbildung 29 Robotik Programm generieren

Dateityp

Dateiname

Quick Start Guide | Visualisierung

### 11.7 Alarmliste

Das rote Dreiecksymbol mit Ausrufezeichen zeigt an, dass ein Fehler aufgetreten ist. Sobald man daraufklickt, öffnet sich eine Liste mit den anstehenden Fehlern. Wurde der Fehler behoben, kann mit den Schaltflächen, der anliegende Fehler quittiert werden

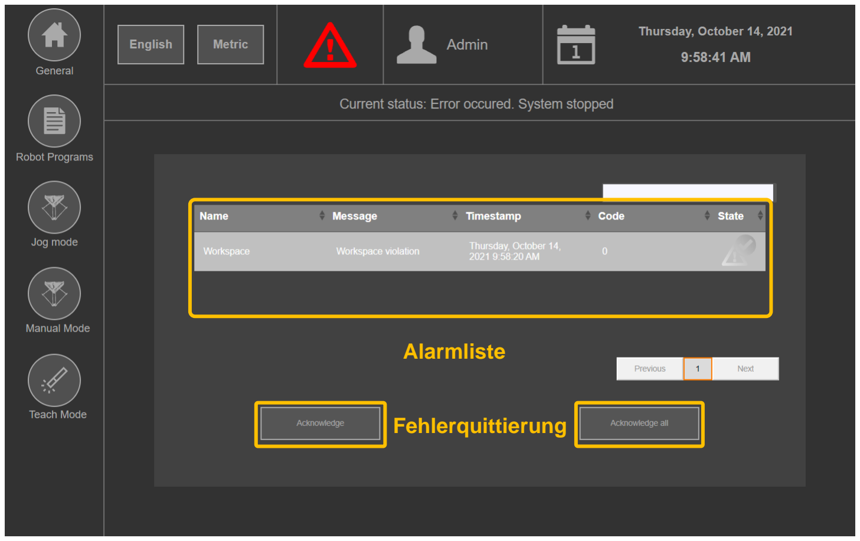
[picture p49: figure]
Alarmliste; Fehlerquittierung

Abbildung 30 Alarmliste

Quick Start Guide | FAQ

## 12 FAQ

### 12.1 ARsim: Trial time expired

Die ARsim kann maximal zwei Stunden durchgehend für Testzwecke benutzt werden. Wird die Testzeit überschritten erscheint diese Meldung. Damit das Programm weiter getestet werden kann muss die ARsim neu gestartet werden.

Abbildung 31 Trial time expired

Quick Start Guide | Abbildungsverzeichnis

## 13 Abbildungsverzeichnis

Abbildung 1 PlotbotDelta | 34
Abbildung 2: Reihenfolge der Hardwaremodule | 7
Abbildung 3: Versorgung SPS und Achse 1 | 9
Abbildung 4: Versorgung Achse 2 und 3 | 10
Abbildung 5 Achsenbezeichnung | 11
Abbildung 6 Motoranschluss | 11
Abbildung 7 Anschluss Referenzschalter | 12
Abbildung 8 Koordinaten Ursprung | 13
Abbildung 9 Mechanische Konfiguration anpassen | 14
Abbildung 10 SceneViewer Modell anpassen | 14
Abbildung 11 B&R Steuerung suchen | 15
Abbildung 12 IP-Adresse ändern | 15
Abbildung 13 Mit Steuerung verbinden | 16
Abbildung 14 Projekt übertragen | 17
Abbildung 15 Übertragungs Einstellungen | 17
Abbildung 16 Roboter Nulllage | 18
Abbildung 17 Projekt aus ARsim übertragen | 19
Abbildung 18 Datei Simulationsmodell | 20
Abbildung 19 SceneViewer Verbindung | 20
Abbildung 20 Verbindungseinstellungen | 20
Abbildung 21 Roboter-Programme | 21
Abbildung 22 Startseite | 23
Abbildung 23 Automatischer Modus | 24
Abbildung 24 Programm Monitor | 25
Abbildung 25 Programm Editor | 26
Abbildung 26 Tippbetrieb | 27
Abbildung 27 Manueller Modus | 28
Abbildung 28 Lern-Modus | 29
Abbildung 29 Robotik Programm generieren | 30
Abbildung 30 Alarmliste | 31
Abbildung 31 Trial time expired | 32

Quick Start Guide | Tabellenverzeichnis

## 14 Tabellenverzeichnis

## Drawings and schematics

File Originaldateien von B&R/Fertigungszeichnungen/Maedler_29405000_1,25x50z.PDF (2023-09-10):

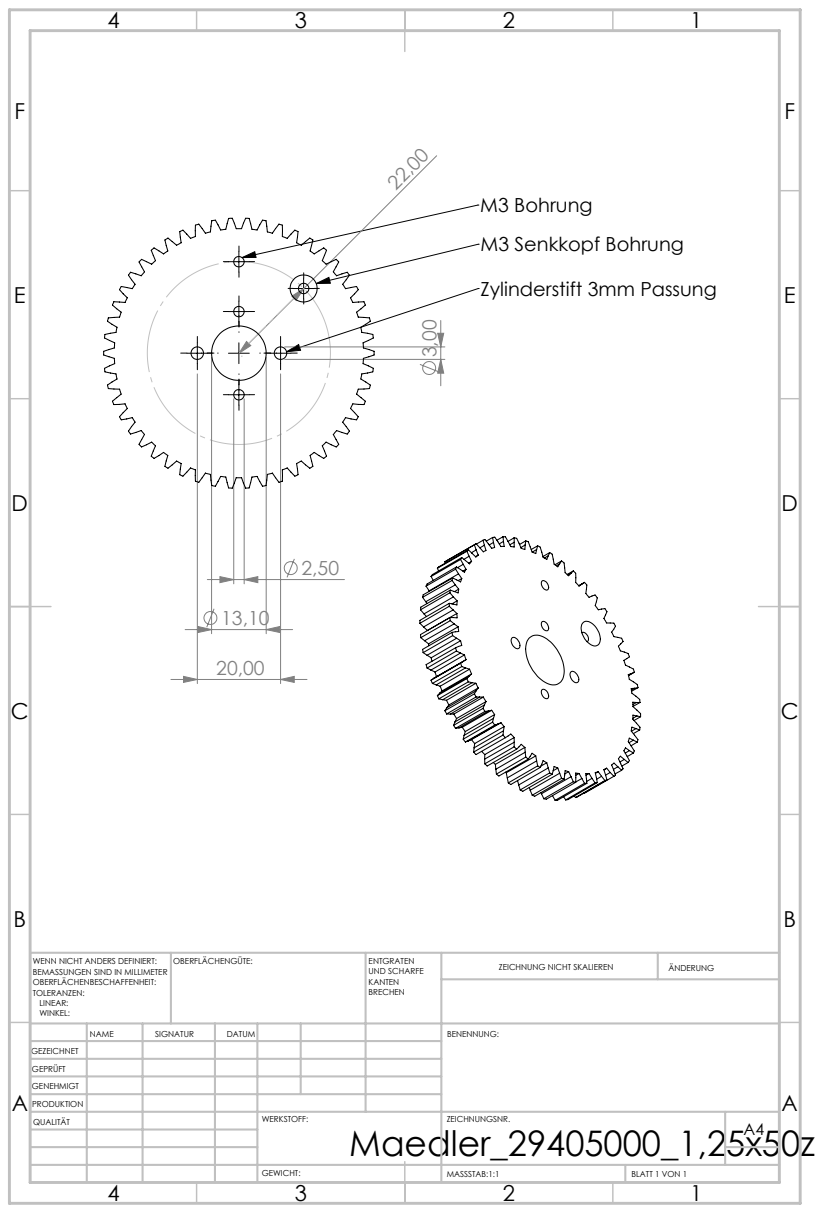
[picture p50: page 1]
M3 Senkkopf Bohrung; M3 Bohrung; Zylinderstift 3mm Passung; MASSSTAB:1:1; BLATT 1 VON 1; ZEICHNUNG NICHT SKALIEREN; ÄNDERUNG; UND SCHARFE; WENN NICHT ANDERS DEFINIERT:; OBERFLÄCHENGÜTE:

BEMASSUNGEN SIND IN MILLIMETER
OBERFLÄCHENBESCHAFFENHEIT:
TOLERANZEN:
LINEAR:
WINKEL:

NAME | SIGNATUR | DATUM | | | | BENENNUNG:
QUALITÄT | | | | WERKSTOFF: Maedler_29405000_1,25x50z GEWICHT: | ZEICHNUNGSNR. | A4

GEZEICHNET
GEPRÜFT
GENEHMIGT
PRODUKTION

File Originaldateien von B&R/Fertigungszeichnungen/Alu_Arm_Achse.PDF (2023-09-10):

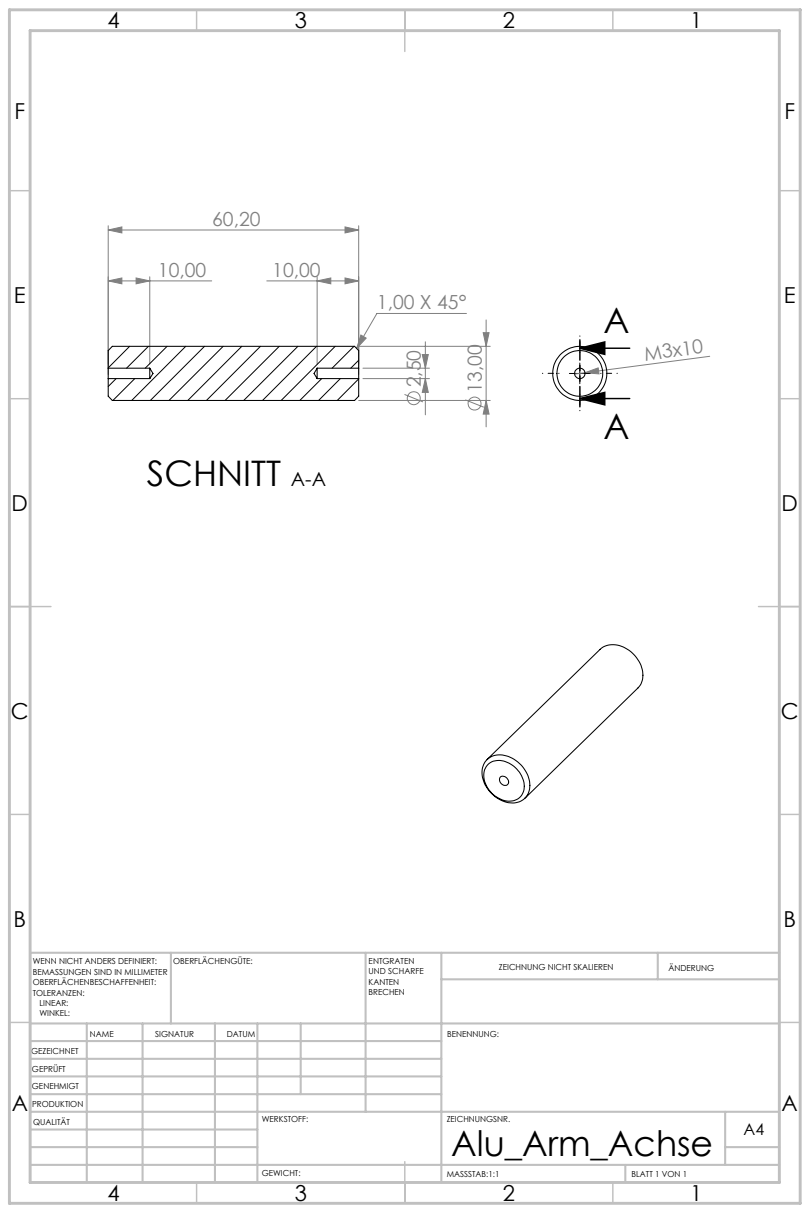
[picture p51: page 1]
SCHNITT A-A; MASSSTAB:1:1; BLATT 1 VON 1; ZEICHNUNG NICHT SKALIEREN; ÄNDERUNG; UND SCHARFE; WENN NICHT ANDERS DEFINIERT:; OBERFLÄCHENGÜTE:

BEMASSUNGEN SIND IN MILLIMETER
OBERFLÄCHENBESCHAFFENHEIT:
TOLERANZEN:
LINEAR:
WINKEL:

NAME | SIGNATUR | DATUM | | | | BENENNUNG:
QUALITÄT | | | | WERKSTOFF: | ZEICHNUNGSNR. Alu_Arm_Achse GEWICHT: | A4

GEZEICHNET
GEPRÜFT
GENEHMIGT
PRODUKTION

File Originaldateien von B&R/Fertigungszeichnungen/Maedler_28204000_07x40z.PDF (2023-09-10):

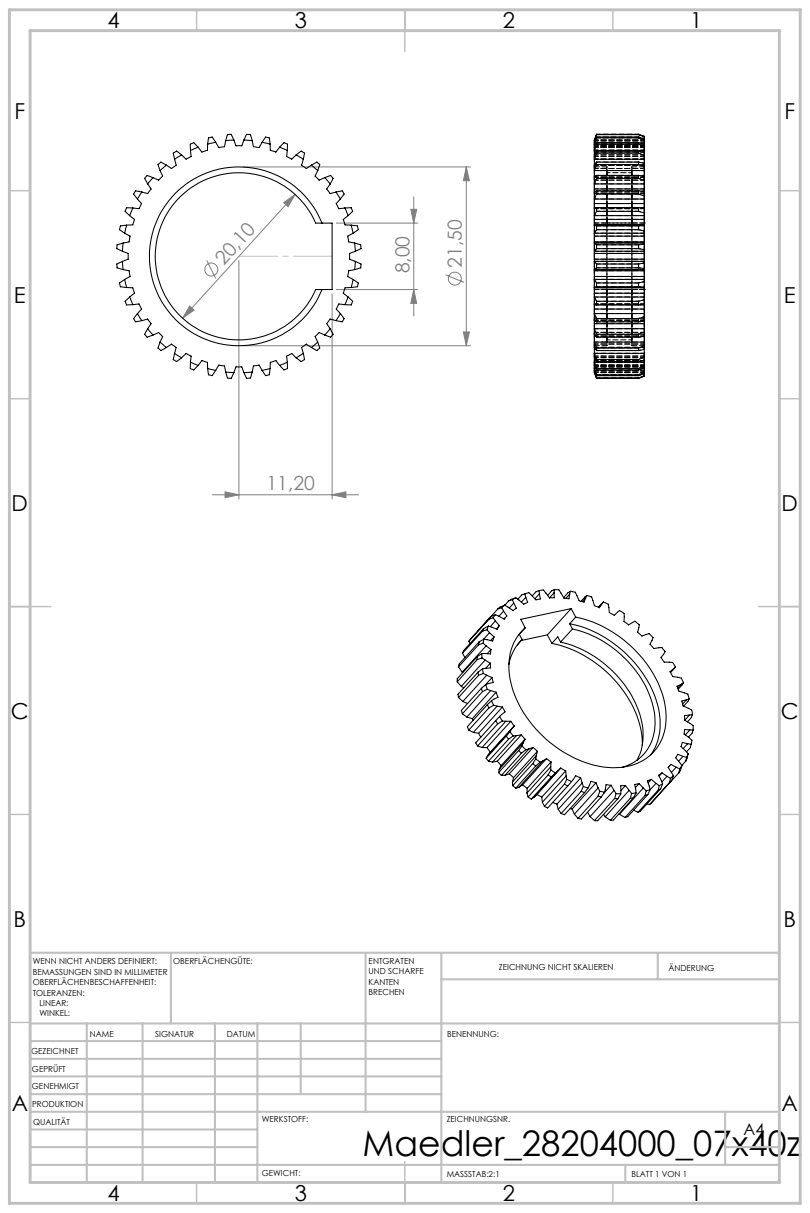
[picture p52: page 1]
MASSSTAB:2:1; BLATT 1 VON 1; ZEICHNUNG NICHT SKALIEREN; ÄNDERUNG; UND SCHARFE; WENN NICHT ANDERS DEFINIERT:; OBERFLÄCHENGÜTE:

BEMASSUNGEN SIND IN MILLIMETER
OBERFLÄCHENBESCHAFFENHEIT:
TOLERANZEN:
LINEAR:
WINKEL:

NAME | SIGNATUR | DATUM | | | | BENENNUNG:
QUALITÄT | | | | WERKSTOFF: Maedler_28204000_07x40z GEWICHT: | ZEICHNUNGSNR. | A4

GEZEICHNET
GEPRÜFT
GENEHMIGT
PRODUKTION

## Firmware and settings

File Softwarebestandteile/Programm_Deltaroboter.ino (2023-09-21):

  const int stepPinX = 2; //X.STEP
  const int stepPinY = 3; //Y.Step
  const int stepPinZ = 4; //Z.Step
  const int stepPinA = 12; //A.STEP
  const int dirPinX = 5; // X.DIR
  const int dirPinY = 6; // Y.DIR
  const int dirPinZ = 7; // Z.DIR
  const int dirPinA = 13; //A.DIR
  #define limitX  9
  #define limitY  10
  #define limitZ  11
  #define Magnet 44  
  const int speed = 400;

 void setup() {

 Serial.begin(115200);
 pinMode(stepPinX,OUTPUT); 
 pinMode(dirPinX,OUTPUT);
 pinMode(stepPinY,OUTPUT); 
 pinMode(dirPinY,OUTPUT);
 pinMode(stepPinZ,OUTPUT); 
 pinMode(dirPinZ,OUTPUT);
 pinMode(stepPinA,OUTPUT); 
 pinMode(dirPinA,OUTPUT);
 pinMode(limitX,INPUT_PULLUP);
 pinMode(limitY,INPUT_PULLUP);
 pinMode(limitZ,INPUT_PULLUP);
 pinMode(Magnet,OUTPUT);
 digitalWrite(Magnet,LOW);
 


  }
 
void home(){
//Home
 digitalWrite(dirPinY,LOW);
 while(digitalRead(limitY) == LOW)
  {
 
 digitalWrite(stepPinY,HIGH); 
 delayMicroseconds(speed); 
 digitalWrite(stepPinY,LOW); 
 delayMicroseconds(speed); 
 }
 digitalWrite(dirPinX,LOW);
 while(digitalRead(limitX) == LOW)
  {
 
 digitalWrite(stepPinX,HIGH); 
 delayMicroseconds(speed); 
 digitalWrite(stepPinX,LOW); 
 delayMicroseconds(speed); 
 }
 digitalWrite(dirPinZ,LOW);
 while(digitalRead(limitZ) == LOW)
  {
 
 digitalWrite(stepPinZ,HIGH); 
 delayMicroseconds(speed); 
 digitalWrite(stepPinZ,LOW); 
 delayMicroseconds(speed); 

 }

 delay(1000);
 if (digitalRead(Magnet) == HIGH){
 magnet_turn();
 }
 return;
}






void magnet_turn(){

 digitalWrite(dirPinA,LOW); 
 for(int x = 0; x < 200; x++) {
 digitalWrite(stepPinA,HIGH);
 delayMicroseconds(2000);
 digitalWrite(stepPinA,LOW);
 delayMicroseconds(2000);
 }
 delay(1000);
  digitalWrite(dirPinA,HIGH); //Changes the rotations direction
 // Makes 400 pulses for making two full cycle rotation
 for(int x = 0; x < 200; x++) {
 digitalWrite(stepPinA,HIGH);
 delayMicroseconds(2000);
 digitalWrite(stepPinA,LOW);
 delayMicroseconds(2000);
 }
 return;
}








void loop (){

home();

//Point 1 take
digitalWrite(dirPinX,HIGH);
digitalWrite(dirPinY,HIGH);
 for(int x = 0; x < 4000; x++) {
 digitalWrite(stepPinX,HIGH);
 digitalWrite(stepPinY,HIGH);
 delayMicroseconds(speed);
 digitalWrite(stepPinX,LOW);
 digitalWrite(stepPinY,LOW);
 delayMicroseconds(speed);
 
 }
 delay(1000);

digitalWrite(dirPinZ,HIGH);
 for(int x = 0; x < 200; x++) {
 digitalWrite(stepPinZ,HIGH);
 delayMicroseconds(speed);
 digitalWrite(stepPinZ,LOW);
 delayMicroseconds(speed);
 }
 digitalWrite(Magnet,HIGH);
delay(1000);
digitalWrite(dirPinX,LOW);
digitalWrite(dirPinY,LOW);
digitalWrite(dirPinZ,LOW);
 for(int x = 0; x < 150; x++) {
 digitalWrite(stepPinX,HIGH);
 digitalWrite(stepPinY,HIGH);
 digitalWrite(stepPinZ,HIGH);
 delayMicroseconds(speed);
 digitalWrite(stepPinX,LOW);
 digitalWrite(stepPinY,LOW);
 digitalWrite(stepPinZ,LOW);
 delayMicroseconds(speed);
 }

home();
 //Point 2 drop
digitalWrite(dirPinZ,HIGH);
digitalWrite(dirPinY,HIGH);
 for(int x = 0; x < 4000; x++) {
 digitalWrite(stepPinZ,HIGH);
 digitalWrite(stepPinY,HIGH);
 delayMicroseconds(speed);
 digitalWrite(stepPinZ,LOW);
 digitalWrite(stepPinY,LOW);
 delayMicroseconds(speed);
 
 }
 delay(1000);

digitalWrite(dirPinX,HIGH);
 for(int x = 0; x < 200; x++) {
 digitalWrite(stepPinX,HIGH);
 delayMicroseconds(speed);
 digitalWrite(stepPinX,LOW);
 delayMicroseconds(speed);
 }
 digitalWrite(Magnet,LOW);
delay(1000);
digitalWrite(dirPinX,LOW);
digitalWrite(dirPinY,LOW);
digitalWrite(dirPinZ,LOW);
 for(int x = 0; x < 150; x++) {
 digitalWrite(stepPinX,HIGH);
 digitalWrite(stepPinY,HIGH);
 digitalWrite(stepPinZ,HIGH);
 delayMicroseconds(speed);
 digitalWrite(stepPinX,LOW);
 digitalWrite(stepPinY,LOW);
 digitalWrite(stepPinZ,LOW);
 delayMicroseconds(speed);
 }
home();
  //Point 2 take
digitalWrite(dirPinZ,HIGH);
digitalWrite(dirPinY,HIGH);
 for(int x = 0; x < 4000; x++) {
 digitalWrite(stepPinZ,HIGH);
 digitalWrite(stepPinY,HIGH);
 delayMicroseconds(speed);
 digitalWrite(stepPinZ,LOW);
 digitalWrite(stepPinY,LOW);
 delayMicroseconds(speed);
 
 }
 delay(1000);

digitalWrite(dirPinX,HIGH);
 for(int x = 0; x < 200; x++) {
 digitalWrite(stepPinX,HIGH);
 delayMicroseconds(speed);
 digitalWrite(stepPinX,LOW);
 delayMicroseconds(speed);
 }
 digitalWrite(Magnet,HIGH);
delay(1000);
digitalWrite(dirPinX,LOW);
digitalWrite(dirPinY,LOW);
digitalWrite(dirPinZ,LOW);
 for(int x = 0; x < 150; x++) {
 digitalWrite(stepPinX,HIGH);
 digitalWrite(stepPinY,HIGH);
 digitalWrite(stepPinZ,HIGH);
 delayMicroseconds(speed);
 digitalWrite(stepPinX,LOW);
 digitalWrite(stepPinY,LOW);
 digitalWrite(stepPinZ,LOW);
 delayMicroseconds(speed);
 }

home();

 //Point 1 drop
digitalWrite(dirPinX,HIGH);
digitalWrite(dirPinY,HIGH);
 for(int x = 0; x < 4000; x++) {
 digitalWrite(stepPinX,HIGH);
 digitalWrite(stepPinY,HIGH);
 delayMicroseconds(speed);
 digitalWrite(stepPinX,LOW);
 digitalWrite(stepPinY,LOW);
 delayMicroseconds(speed);
 
 }
 delay(1000);

digitalWrite(dirPinZ,HIGH);
 for(int x = 0; x < 200; x++) {
 digitalWrite(stepPinZ,HIGH);
 delayMicroseconds(speed);
 digitalWrite(stepPinZ,LOW);
 delayMicroseconds(speed);
 }
 digitalWrite(Magnet,LOW);
delay(1000);
digitalWrite(dirPinX,LOW);
digitalWrite(dirPinY,LOW);
digitalWrite(dirPinZ,LOW);
 for(int x = 0; x < 150; x++) {
 digitalWrite(stepPinX,HIGH);
 digitalWrite(stepPinY,HIGH);
 digitalWrite(stepPinZ,HIGH);
 delayMicroseconds(speed);
 digitalWrite(stepPinX,LOW);
 digitalWrite(stepPinY,LOW);
 digitalWrite(stepPinZ,LOW);
 delayMicroseconds(speed);
 }
}
 

 
 

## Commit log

2023-09-10 B&R Zeug hochladen
    [3x Motorplatte rechts überarbeitet (M3 zur Motormontage).stl, 3x Motorplatte_links_überarbeitet (M3 zur Motormontage).stl, 3x Trägerplatte_Teilstück.STL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]
2023-09-11 Gehäuseteile
    [Gehäuse Elektronik_Deckel.stl, Gehäuse Elektronik_Träger.stl]
2023-09-11 Update Gehäuseträger
    [Gehäuse Elektronik _Träger.stl, Gehäuse Elektronik_Träger.stl]
2023-09-15 Gehäuse Update
    [Gehäuse Elektronik _Träger.stl]
2023-09-18 neue Modelle Motorplatten
    [3x Motorplatte rechts überarbeitet (M3 zur Motormontage).stl, 3x Motorplatte_links_überarbeitet (M3 zur Motormontage).stl]
2023-09-21 Update 3d modelle
    [3xAdapterplatte Motor Planetengetriebe.stl, 3xMotorzahnrad klein 8mm.stl, Motorzahnrad klein SH12521HF.stl]
